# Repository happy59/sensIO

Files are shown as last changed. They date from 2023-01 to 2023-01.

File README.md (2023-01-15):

# SensIO
Here's my upgrade for the Philips Senso. *It should work for any other coffee machine that use push buttons likewise*.
The upgrade is easily reversible. Feel free to take and upgrade this project !
3D print files are available at  [INSERT PRINTABLES LINK](lol%20prout).

I based this project out of a D1miniPro but it can be made with a classic NodeMCU or another ESP board with similar component *(be carefull the D1Mini, even if it has a 5v output, runs on 3,3v)*
## How it works
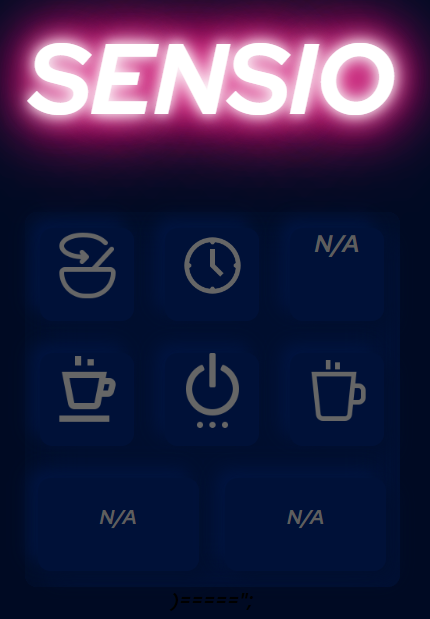
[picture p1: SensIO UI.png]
UI


Using this interface you can :
 - Know if there's a cup
 - Stirr your cup
 - Turn on and off your senseo
 - brew a little or a large cup
 - know the coffee temperature
 - setup a timer for your coffee to be made

## What you need

 - Wemos D1miniPro
 - Few cables
 - 4 relay modules (3v coil)
 - 4 SOT23 A09T MOSFETs
 - 4 diodes
 - Few resistors
	 - 4x100K
	 - 4x1K
	 - 2x10K
 - DIY PCB
	 - If you can't engrave it yourself I suggest you to use a classic breadboard, replacing SOT23 with long legs mosfets
 - 5v source to power the D1mini
	 - I use an old phone charger
 - DC Motor (5V)
 - DS1820 waterproof temperature sensor
 - Sharp IR distance sensor
	 - It's absolutly overkill, any 1/0 laser braking sensor should work
 - 3D printed parts
 - 4 neodymium magnets
 - Few M3 screws
 - Rubber band
## How to do it
Prepare your PCB by soldering all the parts.
This PCB takes place in the spilled coffee tank, you have to drill some holes in it to wire the three buttons. **Don't forget to flash arduino code**, arduino will still be accessible but you'll have to re-open the machine's back to flash it.

Now you can solder wires to the buttons, these welds are pretty easy to do but **be carefull to unplug the machine** the big shiny plate is full of painfull high voltage (trust me, it is). Don't forget the motor cables (not like me), drill through the printed plate.

don't forget thermometer and IR sensor cables, take them to the back. Now you can close the bottom of the machine. Drill a hole for the thermometer and a window to screw the cup sensor. 
I made Y connections from 220v. One branch to the machine and the other to the phone charger. We'll put the phone charger right behind the watertank (safety first 🥴). I wrapped it in thermal sheath to isolate it.

You can put back all the part in place and look at the 3D printed parts.
Put the magnets in their housing. Add a rubber band and tight the magnet pulley in place with M3 screws. And glue the motor with his pulley in place.

Now you'll need to find the machine's IP. You can scan your wifi network with ugly windows commands. I suggest you tu use your rooter interface to find it.
Once you found it *(something like 192.168.X.XX)*, paste the ip in your browser and create a shortcut to it on your phone's desktop. You'll have access to the interface. Et voilà !

I suggest you to create a static IP for your machine. Otherwise, ip can change at each reboot of the rooter. You also can create an aliases for this ip. For exemple when you type "sensIO/" in the browser it'll redirect it to the ip.

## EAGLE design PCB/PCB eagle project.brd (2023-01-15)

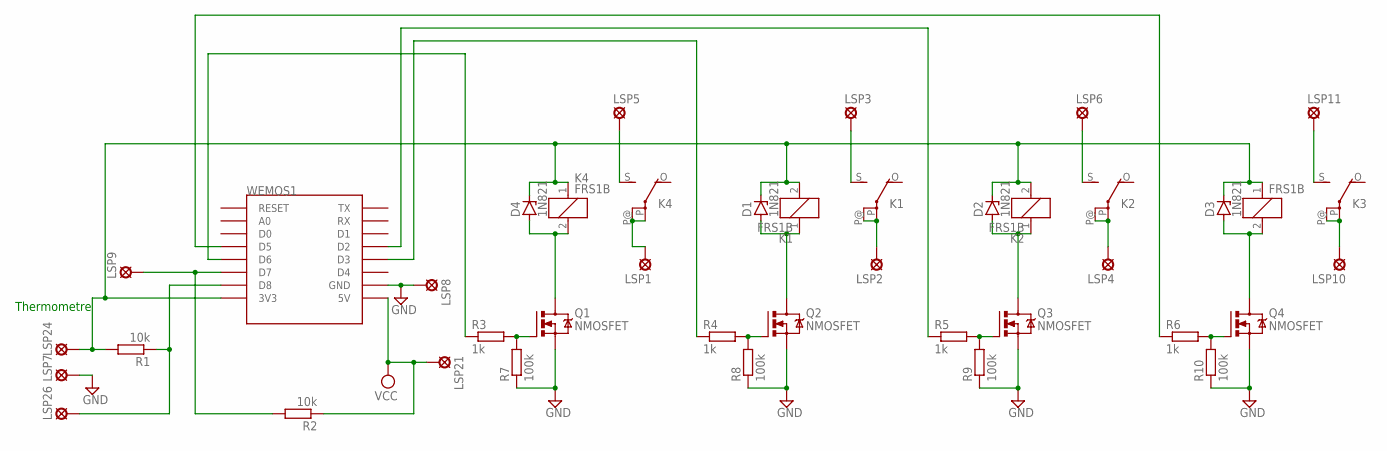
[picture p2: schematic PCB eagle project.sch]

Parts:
D1, D2, D3, D4: 1N821; DO35Z10
K1, K2, K3, K4: FRS1B
LSP1, LSP2, LSP3, LSP4, LSP5, LSP6, LSP7, LSP8, LSP9, LSP10, LSP11, LSP21, LSP24, LSP26: MCS10B
Q1, Q2, Q3, Q4: NMOSFET; SOT23
R1, R2: 10k; 0207/10
R3, R4, R5, R6: 1k; 0207/10
R7, R8, R9, R10: 100k; 0207/10
WEMOS1: ui; WEMOS-D1-MINI

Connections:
GND: LSP7.MP, LSP8.MP, Q1.2 (S), Q2.2 (S), Q3.2 (S), Q4.2 (S), R7.1, R8.1, R9.1, R10.1, WEMOS1.GND
unnamed: K4.S, LSP5.MP
unnamed: K3.S, LSP11.MP
unnamed: K1.S, LSP3.MP
unnamed: K4.P, K4.P@, LSP1.MP
unnamed: K1.P, K1.P@, LSP2.MP
unnamed: LSP26.MP, R1.1, WEMOS1.D8
unnamed: K2.S, LSP6.MP
unnamed: LSP9.MP, R2.2, WEMOS1.D7
unnamed: K2.P, K2.P@, LSP4.MP
unnamed: K3.P, K3.P@, LSP10.MP
unnamed: D1.C, D2.C, D3.C, D4.C, K1.2, K2.2, K3.1, K4.1, LSP24.MP, R1.2, WEMOS1.3V3
unnamed: D4.A, K4.2, Q1.3 (D)
unnamed: D1.A, K1.1, Q2.3 (D)
unnamed: D2.A, K2.1, Q3.3 (D)
unnamed: D3.A, K3.2, Q4.3 (D)
unnamed: Q1.1 (G), R3.2, R7.2
unnamed: Q2.1 (G), R4.2, R8.2
unnamed: Q3.1 (G), R5.2, R9.2
unnamed: Q4.1 (G), R6.2, R10.2
unnamed: R3.1, WEMOS1.D6
unnamed: R4.1, WEMOS1.D3
unnamed: R5.1, WEMOS1.D2
unnamed: R6.1, WEMOS1.D5
VCC: LSP21.MP, R2.1, WEMOS1.5V

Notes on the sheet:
Thermometre

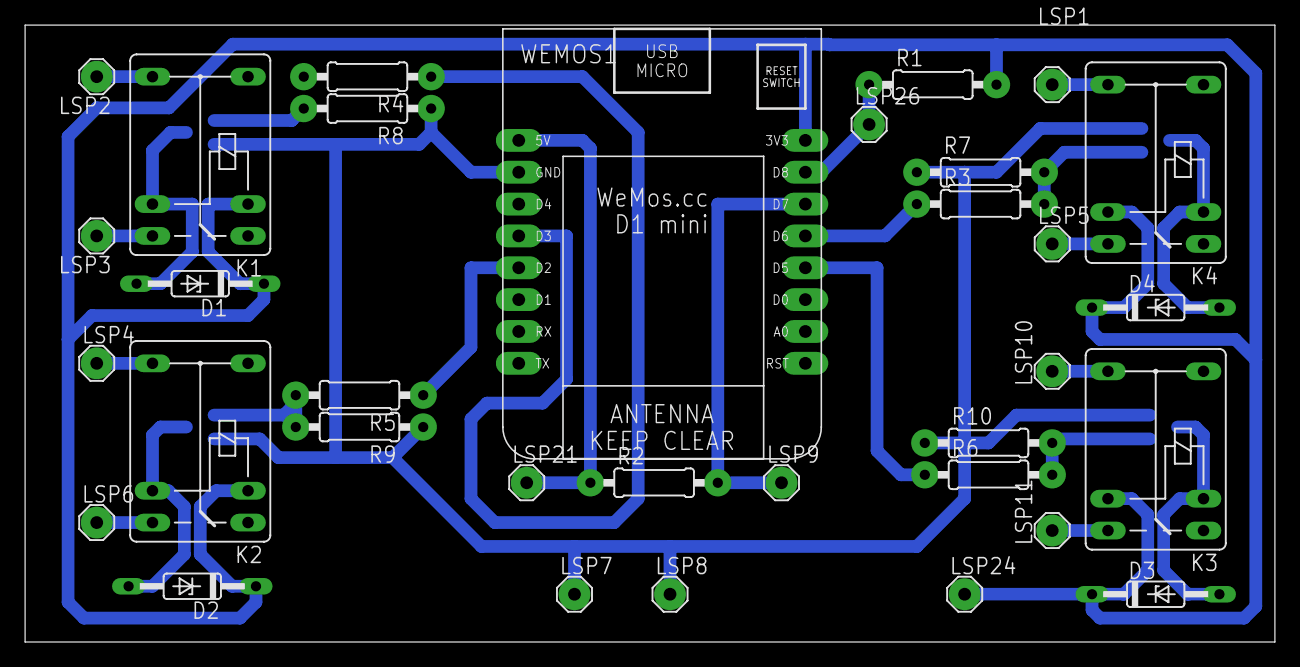
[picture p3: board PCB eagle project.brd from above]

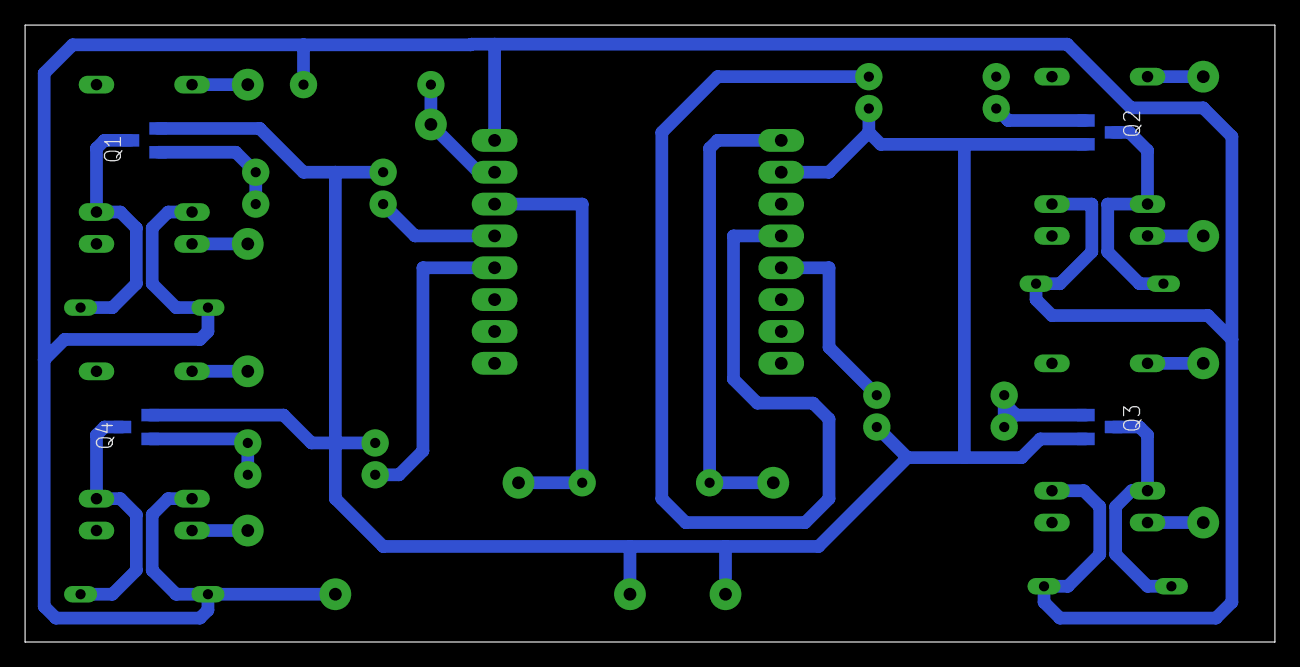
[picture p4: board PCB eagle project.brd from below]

Board: 2 copper layers, 99.7 x 49.2 mm, 37 parts (4 on the bottom side), 25 nets.

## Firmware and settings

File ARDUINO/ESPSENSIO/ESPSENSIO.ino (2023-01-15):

#include <ESP8266WiFi.h>
#include <WiFiClient.h>
#include <ESP8266WebServer.h>
#include <OneWire.h>
#include <DallasTemperature.h>

#include "index2.h" //Our HTML webpage contents with javascripts

#define pinCapteurTasse D7 //pin module Sharp
#define moteur D6 //relay du moteur
#define sortiePTasse D3 //bouton petite tasse
#define sortieGTasse D2 //bouton grosse tasse
#define power D5 //bouton ONOFF

#define ONE_WIRE_BUS D1
#define TEMPERATURE_PRECISION 10
// Setup a oneWire instance to communicate with any OneWire devices (not just Maxim/Dallas temperature ICs)
OneWire oneWire(ONE_WIRE_BUS);
// Pass our oneWire reference to Dallas Temperature.
DallasTemperature sensors(&oneWire);
// Tableaux contenant l'adresse de chaque sonde OneWire | arrays to hold device addresses
DeviceAddress insideThermometer = { 0x28,  0x6D,  0xFB,  0x96,  0xF0,  0x1,  0x3C,  0xFD };

//SSID and Password of your WiFi router
const char* ssid = "[ENTER YOUR SSID]"; const char* password = "[ENTER YOUR PASSWORD]";
bool enTouillage = false;
bool etat = true;

ESP8266WebServer server(80); //Server on port 80

//===============================================================
// This routine is executed when you open its IP in browser
//===============================================================
void handleRoot() {
  String s = MAIN_page; //Read HTML contents
  server.send(200, "text/html", s); //Send web page
}

void handleTasse() {
  String tasse = "0";
  if (digitalRead(pinCapteurTasse) == LOW) {
    tasse = "0";

  }
  else if (digitalRead(pinCapteurTasse) == HIGH) {
    tasse = "1";

  }
  delay(50);
  server.send(200, "text/plane", tasse); //Send tasse value only to client ajax request
}

void handleTemp() {
  sensors.requestTemperatures();
  float temp = sensors.getTempC(insideThermometer);
  String tempString = (String)temp + "°C";
  Serial.println(tempString);
  //Serial.println(tempString);
  delay(50);
  server.send(200, "text/plane", tempString); //Send ADC value only to client ajax request
}

void handleEtat(){
  String retour = "N/A";
  if(etat==true){retour = "allume";}
  else{retour = "eteint";}
  delay(50);

  server.send(200, "text/plane", retour);
}

void handleTouillage(){
  String aEnvoyer = "N/A";
  if(enTouillage){aEnvoyer = "allume";}  
  else{aEnvoyer = "eteint";}

  delay(50);
  server.send(200, "text/plane", aEnvoyer);
}

void allumeMachine() 
{
 String boutonAppuye = server.arg("state");
 if(boutonAppuye == "0")//Bouton Power
 {
  etat = !etat;
  digitalWrite(power, HIGH); //LED ON
  delay(500);
  digitalWrite(power, LOW);
 }
 if(boutonAppuye == "1")//Bouton PT
 {
  digitalWrite(sortiePTasse, HIGH); //LED ON
  delay(500);
  digitalWrite(sortiePTasse, LOW);
 }
 if(boutonAppuye == "2")//Bouton GT
 {
  digitalWrite(sortieGTasse, HIGH); //LED ON
  delay(500);
  digitalWrite(sortieGTasse, LOW);
 }
 if(boutonAppuye == "3")//Bouton stir
 {
  if(enTouillage == false){digitalWrite(moteur, HIGH); enTouillage = !enTouillage;}
  else {digitalWrite(moteur, LOW); enTouillage = !enTouillage;}
 }
 if(boutonAppuye == "4"){
  faitLCaf();
 }

 server.send(200);
}

void faitLCaf(){
  if(!etat){
    etat = !etat;
    digitalWrite(power, HIGH); //LED ON
    delay(500);
    digitalWrite(power, LOW);    
  }
  
  if(digitalRead(pinCapteurTasse) == HIGH){
    delay(90000);
    digitalWrite(sortiePTasse, HIGH); //LED ON
    delay(500);
    digitalWrite(sortiePTasse, LOW);
    delay(20000);
  }
  etat=!etat;
  digitalWrite(power, HIGH); //LED ON
  delay(500);
  digitalWrite(power, LOW);
}

//==============================================================
//                  SETUP
//==============================================================
void setup(void) {
  Serial.begin(115200);

  // Start up the library
  sensors.begin();

  // locate devices on the bus
  Serial.print("Locating devices...");
  Serial.print("Found ");
  Serial.print(sensors.getDeviceCount(), DEC);
  Serial.println(" devices.");

  // report parasite power requirements
  Serial.print("Parasite power is: ");
  if (sensors.isParasitePowerMode()) Serial.println("ON");
  else Serial.println("OFF");

  // Vérifie si les capteurs sont connectés | check and report if sensors are conneted
  if (!sensors.getAddress(insideThermometer, 0)) Serial.println("Unable to find address for Device 0");//On parle du thermomètre là

  // set the resolution to 9 bit per device
  sensors.setResolution(insideThermometer, TEMPERATURE_PRECISION);


  // On vérifie que le capteur st correctement configuré | Check that ensor is correctly configured
  Serial.print("Device 0 Resolution: ");
  Serial.print(sensors.getResolution(insideThermometer), DEC);
  Serial.println();

  WiFi.begin(ssid, password);     //Connect to your WiFi router
  Serial.println("");

  //Réglage des pin (GPIO)
  pinMode(pinCapteurTasse, INPUT);
  pinMode(sortiePTasse, OUTPUT);
  pinMode(sortieGTasse, OUTPUT);
  pinMode(power, OUTPUT);
  pinMode(moteur, OUTPUT);

  digitalWrite(power, LOW);
  digitalWrite(sortiePTasse, LOW);
  digitalWrite(sortieGTasse, LOW);
  digitalWrite(moteur, LOW);
  

  // Wait for connection
  while (WiFi.status() != WL_CONNECTED) {
    delay(500);
    Serial.print(".");
  }

  //If connection successful show IP address in serial monitor
  Serial.println("");
  Serial.print("Connected to ");
  Serial.println(ssid);
  Serial.print("IP address: ");
  Serial.println(WiFi.localIP());  //IP address assigned to your ESP

  server.on("/", handleRoot);      //Which routine to handle at root location. This is display page
  server.on("/readTasse", handleTasse);
  server.on("/readTemp", handleTemp);
  server.on("/allumage", allumeMachine);
  server.on("/readEtat", handleEtat);
  server.on("/readTouillage", handleTouillage);
  

  server.begin();                  //Start server
  Serial.println("HTTP server started");
}



//==============================================================
//                     LOOP
//==============================================================
void loop(void) {
  server.handleClient();          //Handle client requests

}

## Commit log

2023-01-15 Adding arduino files for the D1MiniPro
2023-01-15 Putting .ino file in a folder. Added CAM files for PCB Added screenshot of SensIO UI
